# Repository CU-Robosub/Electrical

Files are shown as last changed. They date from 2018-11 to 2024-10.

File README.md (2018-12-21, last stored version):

# Electrical
All PCBs for the CU Boulder RoboSub team along with datasheets and archives from previous years.
### Datasheets
Collection of datasheets for all major PCB components
### Electrical_Archive
PCB Schematics, Layouts, and Libraries from previous years
### Hydrophone_Board
Design documents for the Hydrophone Board
### Merge_ESC_Board
Design documents for the Merge/ESC Board
### Power_Embedded_Board
Design documents for the Power/Embedded System Board
### Pneumatics_Board
Design documents for the Pneumatics Actuator Board
### Libraries
All Schematic, Footprint, and Integrated Libraries for the boards

## Merge/ESC Board Datasheet Links
Merge/ESC board will contain the Merge Circuit and header plugs for the Pololu along with outputs for the PWM and power outputs for the Electronic Speed Controllers.
### Merge Circuit
1. [LTC4357 Datasheet](http://cds.linear.com/docs/en/datasheet/4357fd.pdf)
2. [IPT004 Datasheet](https://www.infineon.com/dgdl/Infineon-IPT004N03L-DS-v02_00-EN.pdf?fileId=db3a30433e9d5d11013e9e0f382600c2)
### Current Monitor
1. [AD8217 Datasheet](http://www.analog.com/media/en/technical-documentation/data-sheets/AD8217.pdf)
### Kill Switch
1. [IRLR6225 Datasheet](https://www.infineon.com/dgdl/irlr6225pbf.pdf?fileId=5546d462533600a40153566d99bc26c1)

## Power/Embedded Board Datasheet Links
### 5V Converter
1. [R-78E5-0.5 Datasheet](https://www.recom-power.com/pdf/Innoline/R-78Exx-0.5.pdf) 
2. [AD8217 Datasheet](http://www.analog.com/media/en/technical-documentation/data-sheets/AD8217.pdf)
### 12V Converter
1. [Digikey](https://www.digikey.com/product-detail/en/tdk-lambda-americas-inc/I6A4W020A033V-003-R/285-2669-ND/6605122)
2. [Datasheet](https://www.us.tdk-lambda.com/ftp/specs/i6a4w_datasheet.pdf)
### 9V and 19V Converter
1. [LTC3780 Datasheet](http://cds.linear.com/docs/en/datasheet/3780ff.pdf)
2. [LTC3780 LTSpice](http://www.linear.com/product/LTC3780)
3. [BUK6212 Datasheet](https://assets.nexperia.com/documents/data-sheet/BUK6212-40C.pdf)
4. [MMSZ5230B Datasheet](https://www.diodes.com/assets/Datasheets/ds18010.pdf)
5. [MBRS340 Datasheet](https://www.mouser.com/ds/2/308/MBRS340-1120985.pdf)
6. [IN5819 Datasheet](http://www.kesenes.com/pdf/1n5817-1n5819.pdf)
7. [SRR1240 Datasheet](https://www.bourns.com/docs/Product-Datasheets/SRR1240.pdf)
8. [AD8217 Datasheet](http://www.analog.com/media/en/technical-documentation/data-sheets/AD8217.pdf)
### 48V Converter
1. [LTC3958 Datasheet](https://www.analog.com/media/en/technical-documentation/data-sheets/3958fa.pdf)
2. [LTC3958 LTSpice](http://www.linear.com/product/LT3958)
3. [IHLP-6767DZ-11 Datasheet](http://www.vishay.com/docs/34306/lp67dz11.pdf)
4. [AD8217 Datasheet](http://www.analog.com/media/en/technical-documentation/data-sheets/AD8217.pdf)
5. [MBRS360](https://www.onsemi.com/pub/Collateral/MBRS360T3-D.PDF)
### Embedded System
1. [MSP432P401R](http://www.ti.com/lit/ds/symlink/msp432p401r.pdf)
2. [DMN1019USN](https://www.diodes.com/assets/Datasheets/DMN1019USN.pdf)
3. [RGB LED Strip](https://www.sparkfun.com/products/12021)
4. [R-78E3.3-1.0](https://www.recom-power.com/pdf/Innoline/R-78Exx-1.0.pdf)
5. [JTAG Connector Digikey](https://www.digikey.com/product-detail/en/samtec-inc/FTSH-105-01-L-DV-K-TR/SAM13165CT-ND/8827920)
6. [JTAG Connector Datasheet](http://suddendocs.samtec.com/prints/ftsh-1xx-xx-xxx-dv-xxx-xxx-mkt.pdf)
7. [FTDI FT230X](https://www.ftdichip.com/Support/Documents/DataSheets/ICs/DS_FT230X.pdf)
8. [ABS25 Crystal Low Freq](https://abracon.com/Resonators/abs25.pdf)
9. [ABLS Crystal High Freq](https://abracon.com/Resonators/abls.pdf)
10. [Push Button Digikey](https://www.digikey.com/product-detail/en/te-connectivity-alcoswitch-switches/FSM101/450-1157-ND/701084)

## Pneumatics Board Datasheet Links
1. [MSP432P401R](http://www.ti.com/lit/ds/symlink/msp432p401r.pdf)
2. [JTAG Connector Digikey](https://www.digikey.com/product-detail/en/samtec-inc/FTSH-105-01-L-DV-K-TR/SAM13165CT-ND/8827920)
3. [JTAG Connector Datasheet](http://suddendocs.samtec.com/prints/ftsh-1xx-xx-xxx-dv-xxx-xxx-mkt.pdf)
4. [ABS25 Crystal Low Freq](https://abracon.com/Resonators/abs25.pdf)
5. [ABLS Crystal High Freq](https://abracon.com/Resonators/abls.pdf)
6. [FDY300NZ](https://www.fairchildsemi.com/datasheets/FD/FDY300NZ.pdf)
7. [R-78E3.3-1.0](https://www.recom-power.com/pdf/Innoline/R-78Exx-1.0.pdf)

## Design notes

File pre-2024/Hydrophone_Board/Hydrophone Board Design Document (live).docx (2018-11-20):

# CU RoboSub team

CU Robosub team

(date of release)

Hydrophone board

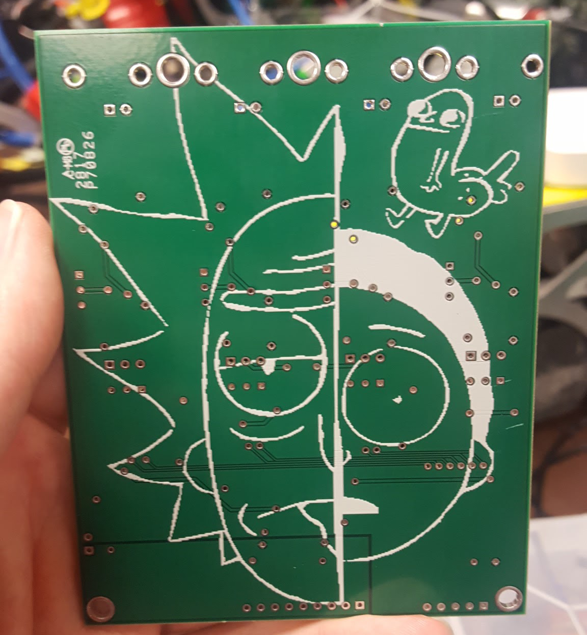
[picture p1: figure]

# Index

Abstract 3

Design Requirements 3

Design Overview 3

Previous designs 3

System Implementations 4

Power System 4

Active Filter 4

Amplification stage 4

ADC Sampling 4

System status 4

Known Issues 4

Appendix 4

# Abstract

This document will describe the standard documentation elements for the electrical design team. It is broken up into multiple sections that can be used or not used as is need. There will be release versions of this document as well as a “live” version. Release versions will be prefixed with the date of release (ie 2018-3-6-design-document-Format.pdf) and will be exported as PDF files. By keeping a live and release versions available members will continually be able to change, append, and add sections as is needed. Release versions will be tied to a particular version of the board that is manufactured.

# Design Requirements

In this section the requirements for each board will be described. This can be done with:

- Bullet points
- That describe each requirements

Description | Specifications
Or with a table | That can go into much greater detail about individual needs for each requirement

# Design Overview

This section will give the overall description of how all the different systems on the board work together. Not going into great detail on each individual section but any seasoned electrical engineer should be able to understand the entire system from this section alone.

## Previous designs

This section will give a high level description of previous designs and what was changed with this version. For new boards this is not necessary but for any revisions it will be required to look at previously released documentation and provide a description of which (if any) systems have been changed. If no systems have been changed describe why the board is being re-made.

# System Implementations

These sections will be made up of the technical information about each sub system. They should be sufficiently descriptive for a novice electrical engineering to be able to reference the information provided to learn how the systems work. This is the Section where you find the most errors in your work because as you try to justify your design decisions you may realise that you have made some incorrect assumptions. It will also give the team lead who will review this the opportunity to check on your thought process and make sure you are making the right design choices

## Power System

Basic LDO stage for getting needed power rails for adc, and filter stage

## Active Filter

Since the

## Amplification stage

Information about that

## ADC Sampling

Information about the Maxim board

# System status

This section is dedicated to describing the status of the system. What version is it on where is it in the production schedule.

# Known Issues

The board did not sample properly due to an issue with grounding of the negative line of the

# Appendix

This is where you will store all of your information on which parts were used and links to their data sheets. Also links to where the Altium files can be found (they should be within the folder this document is stored in) and any citations to resources you found useful in the design process for this part.

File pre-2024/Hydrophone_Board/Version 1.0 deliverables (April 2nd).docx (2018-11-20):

- Board schematics: complete
- Design document: incomplete
  - Abstract incomplete
  - Design requirements incomplete
  - Design Overview incomplete
  - Previous design incomplete
    - Hydrodynamix
  - Implementations incomplete
    - Power System incomplete
      - Schematic
      - Part descriptions
    - Active Filter incomplete
      - Filter response diagrams
      - Part selection
    - Amplification stage incomplete
      - Part selection
      - Gain choice
      - Gain switching chip
    - ADC sampling incomplete
      - MAXIM 11043
      - Reference the design choices
  - Known issues incomplete
    - Many lol
  - Appendix incomplete
    - Reference parts
    - Reference Python package
    - Reference fpga project

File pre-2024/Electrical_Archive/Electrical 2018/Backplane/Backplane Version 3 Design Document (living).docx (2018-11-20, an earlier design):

CU RoboSub Team

8/15/2018

Backplane V3

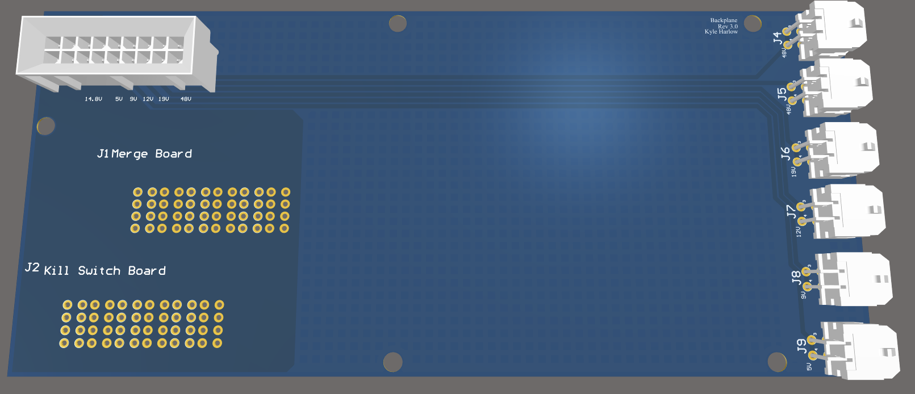
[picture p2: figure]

Abstract 3

Design Requirements 3

Design Overview 3

Previous designs 3

System descriptions 4

System status 4

Known Issues 4

Appendix 5

# Abstract

The backplane supports all of the other PCBs attached to it and properly routes power to those boards. The backplane also routes power to all other systems on the sub through a variety of headers and passive components.

# Design Requirements

Using a variety of molex connectors, passive traces, and polygon planes, the backplane must:

- Receive input power and ground connections from the merge board.
- Route proper connections for power and ground to every other board without thermal issues.
- Export the power board’s voltage lines to an accessible place in the sub, so wires can be routed to proper locations.

# Design Overview

This entirely passive board will use molex connectors and heavier copper pours to achieve all design requirements listed above. The Merge Board and ESC Board will connect using Molex’s EXTreme EnergetiC Modular Right-Angle and Vertical Plug Assemblies since they only need to pass a lot of power between each other. The Power Board will connect to the backplane through Molex’s Micro-Fit BMI Dual Row Receptacle Header with 18 pins because it has to pass several voltage lines as well as receive enough power and ground connections for proper power delivery. For the conversion from PCB traces to wires, we used the 4 pin Molex MiniFit Juniors at the end of the power board. Despite their size, these can handle the current requirements our systems need, and with their locking clips, they provide safe connections to the rest of the system.

## Previous designs

Previous designs of the backplane had no major issues, but the change to better connectors required a redesign. This redesign also allowed us to switch to higher oz copper which was a long term plan to allow for better thermals.

# System descriptions

Shown below is the completed backplane in Altium. Red represents top layer traces while blue represents bottom level traces. To properly route power without overheating, this board was manufactured with 6oz copper, which physically compresses more copper onto the pcb traces and planes so it takes longer to heat up. This increase of copper allows for smaller trace widths from the power board connector, at the top of the picture, to the molex connectors, at the far right of the picture.

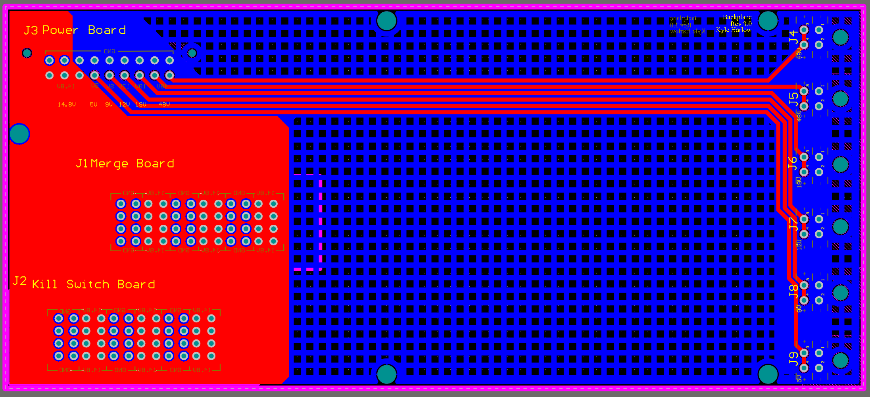
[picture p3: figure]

Due to this board being entirely passive and still quite large, the ground plane, on the bottom layer, was latticed in unused areas. This reduces the amount of wasted copper while still providing proper connections, resistance from warping, and some noise shielding. Besides the molex vias, full standoff screw holes were created for proper usage in the sub on the electrical rack. This was mainly for support and rigidity since none of the electrical rack was conductive.

# System status

This system was completed and ran successfully on the 2018 sub Leviathan. No major issues were experienced after soldering.

# Known Issues

- Board potentially not needed. If kill switch/esc board is removed, the molex connectors can be moved to the power and merge boards to save cost and space. The power and merge boards can then be directly connected to transfer power properly.
- Incorrect via sizes for molex headers
- Wrong initial orientation of power board’s header
- Molex connectors do not provide enough support to boards without electrical rack

# Appendix

Backplane MiniFit Juniors - https://www.molex.com/molex/products/datasheet.jsp?part=active/0039300040_PCB_HEADERS.xml

Power Board Micro-Fit - https://www.molex.com/molex/products/datasheet.jsp?part=active/0447640801_PCB_RECEPTACLES.xml

Merge and ESC - https://www.molex.com/molex/products/datasheet.jsp?part=active/1721860010_PCB_RECEPTACLES.xml

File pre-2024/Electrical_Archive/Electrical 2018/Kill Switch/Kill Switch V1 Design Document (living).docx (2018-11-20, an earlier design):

# CU Robosub team

# 8/29/2018

# Kill Switch/ESC Board

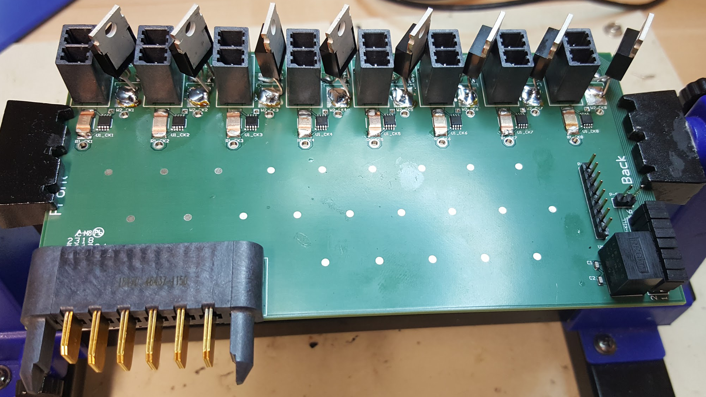
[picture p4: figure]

Abstract 3

Design Requirements 3

Design Overview 3

Previous designs 3

System descriptions 3

Recom and Kill Switch 4

System status 4

Known Issues 5

Appendix 5

# Abstract

The kill switch board controls all power to the ESC modules and therefore the motors. This board can cut the power to the motors based off the kill switch’s state, allowing voltage to pass through the onboard mosfets to ground or holding the voltage high so the motors have nothing to work off of.

# Design Requirements

The kill switch board must:

- Receive input power and ground connections from the backplane.
- Route proper connections for power and ground to every ESC module.
- Use the kill switch’s state to properly turn off the motors.
- Not overheat from the amount of current passing through it.

# Design Overview

All of the ESC modules are controlled by N-channel mosfets that had their gate connected to a 5V line which could be broken by the kill switch. The mosfet’s controlled the motor’s connection to ground, so if the kill switch was active, then the motors would float at 14.8V with no way to draw current and turn. When the kill switch was disabled, the 5V line would activate the mosfets which allowed the motors to create a complete circuit and rotate as desired by the Pololu controller.

## Previous designs

Previously, this board was combined with the merge board due to the power requirements of the motors and the sub. The previous design was functional, but there was too much power on that pcb, without proper thermal considerations, so it started melting off soldered components. The mosfets also were not reliable and several broke from various incidents of polarity and misuse.

# System descriptions

Shown below is the completed kill switch board design. Red represents top layer traces while blue represents bottom level traces. This board ended up being a four layer PCB in order to route power and ground planes more efficiently and to potentially improve thermals with extra copper pours.

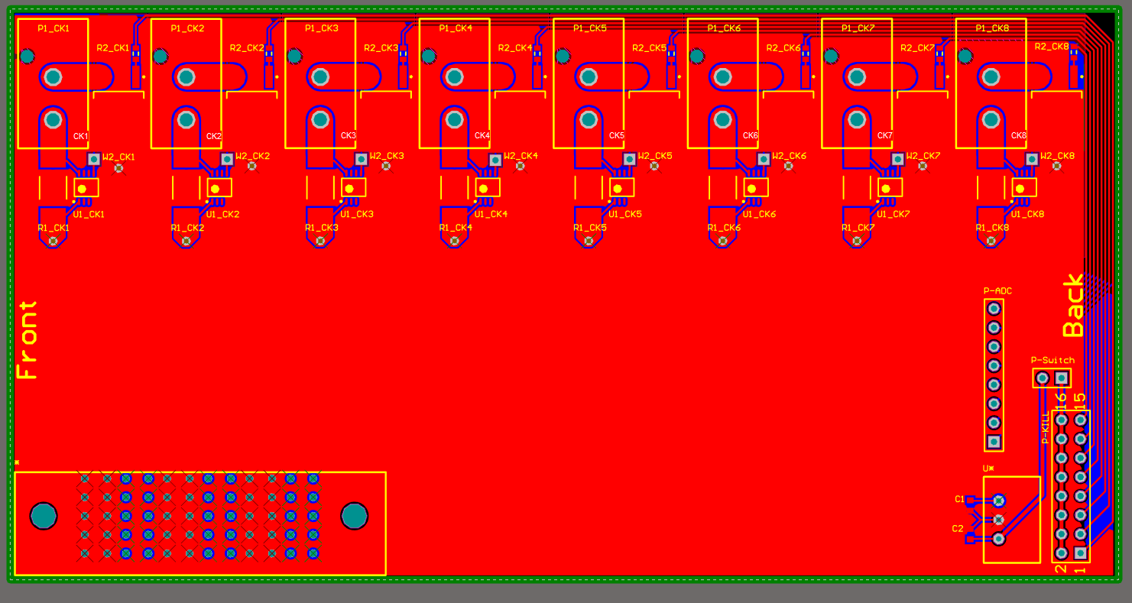
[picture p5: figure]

The top two layers of this board were reserved for the ground plane so that the mosfets could easily connect to the plane and pass as much current to it as needed. These planes were connected through a lattice of vias, not shown in the picture, to assure proper connections and thermal availability. The bottom two layers were set as the power plane that connected to the through-hole molex connectors. These connectors were for the ESC’s to connect to in a polarized way that couldn’t reverse polarity on accident like the previous bullet connectors. These bottom two planes were connected by more latticed vias to assure proper power distribution throughout the board. AD8217s were used as current monitors for the ESC inputs.

## Recom and Kill Switch

In the bottom right corner of this board a recom 5V converter was provided to create a gate signal for all of the mosfets. This voltage line immediately connected to the kill switch so that we could control the gate signals. The kill switch was soldered between the two horizontal vias labeled as p-switch. From the other end of the killswitch we created a row of jumper headers to connect all of the gates to the signal in an easy way. Due to the Recom’s max current specs and good electrical practices, we also implemented 1KOhm resistors in series in front of the gates to not kill the mosfets if any power spikes did occur for any reason.

# System status

This system was completed and ran successfully on the 2018 sub Leviathan. No major issues were experienced after soldering.

# Known Issues

- This board is potentially not needed. Due to the Pololu Motor Controller’s reset pin, we can cut all motors without this board. Resetting the Pololu will remove all data inputs for the ESC’s and they will stop providing power to the motors.
- Wrong mosfet connections. Flip source and drain routing for proper function
- Schematics only show boxes for the mosfets instead of their internal design. (This created the wrong mosfet orientation problem)
- Forgotten pulldown resistor from mosfet gates to GND
- Kill Switch soldering vias were easily stripped/deplated. Switch to Molex connectors

# Appendix

N-Channel Mosfets: https://www.digikey.com/product-detail/en/infineon-technologies/IRLR6225TRPBF/IRLR6225TRPBFCT-ND/2538170

5V converter: https://www.digikey.com/product-detail/en/recom-power/R-78E5.0-0.5/945-1648-5-ND/2834904

ESC Connectors:

https://www.molex.com/molex/products/datasheet.jsp?part=active/0768290102_PCB_HEADERS.xml

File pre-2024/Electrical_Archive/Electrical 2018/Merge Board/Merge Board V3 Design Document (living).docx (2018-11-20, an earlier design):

# CU Robosub team

# 9/1/2018

# Merge Board

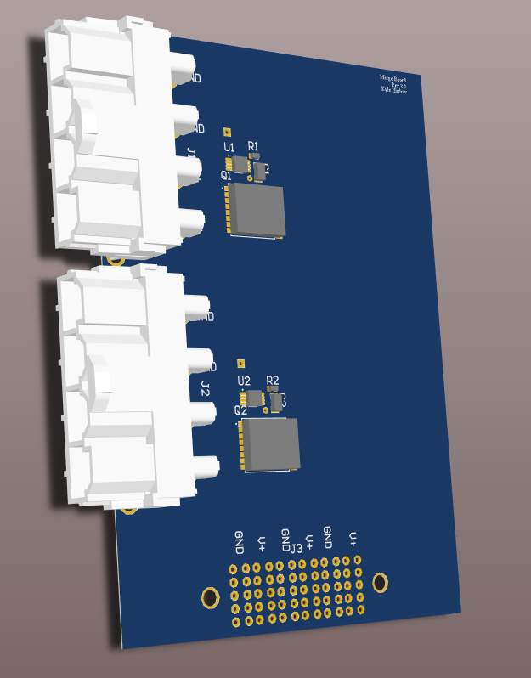
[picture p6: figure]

Abstract 3

Design Requirements 3

Design Overview 3

Previous designs 3

System descriptions 4

System status 5

Known Issues 5

Appendix 5

# Abstract

The merge board controls all input power to the sub from the two batteries. This board also balances the battery draw so that they drain equally and don’t start charging each other or dropping too quickly into dangerous low voltage states.

# Design Requirements

The merge board must:

- Receive input power and ground connections from the battery pods.
- Route proper connections for power and ground to the backplane.
- Not overheat from the amount of current passing through it.

# Design Overview

The batteries connect to the merge board through Molex CONNECTORS that can handle the large amount of current flowing through them. From there, the batteries are funnelled through high power mosfets from Infineon Technologies that can be turned off by commands from LTC4357s. The two LTC4357s perform OR operations to use the battery with the highest voltage, so that the sub will drain the fullest battery first. From there, the two battery inputs are merged into a 3oz copper plane and connected to the backplane for the other systems to use.

## Previous designs

Old merge boards used to combine both the kill switch/esc board and the merge board. This was to save space and cost, but due to oversights in copper thickness and design, these boards did not work as intended. Old desings had too small of copper necks from the battery connectors to the high power mosfets, so they would significantly heat up and potentially melt components off of the board. The old designs also used unreliable connectors to attach the battery leads which created worries for shorting and current throughput.

# System descriptions

Shown below is the completed kill switch board design. Red represents top layer traces while blue represents bottom level traces. This board ended up being a two layer PCB with 3oz copper pours in order to route power and ground planes more efficiently and to significantly improve thermals. While it would have been better, 6oz copper was not used due to the clearances the LTC4357 and mosfet’s pads need to work properly. To compensate for this, large power and ground planes were used to dissipate the extra heat.

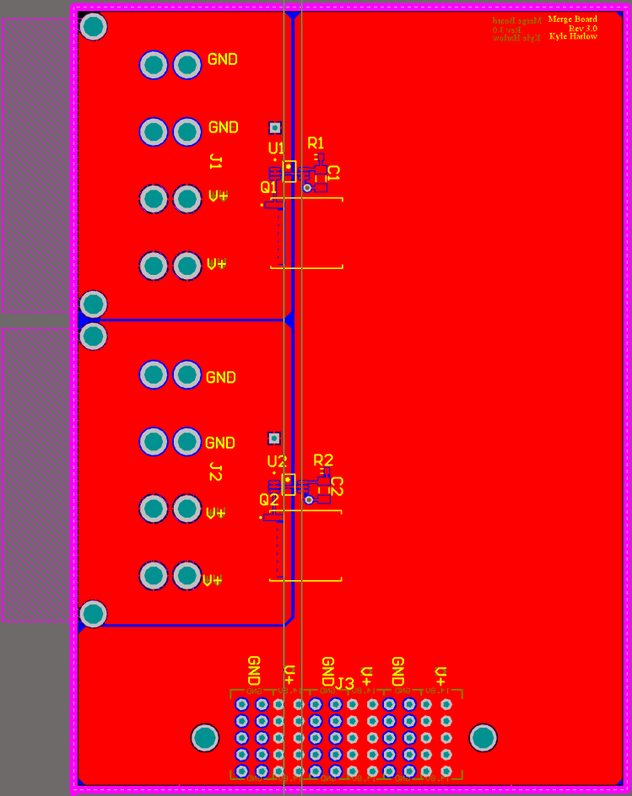
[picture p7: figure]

# System status

This system was completed and ran successfully on the 2018 sub Leviathan. No major issues were experienced after soldering.

# Known Issues

- This board is too tall. With the electrical rack, the clearance from this board to the acrylic tube is small enough to cause issues when taking the sub apart.
- The connector to the backplane cannot support the board completely and will get looser overtime.

# Appendix

Input Mosfets: https://www.digikey.com/products/en?keywords=IPT004N03LATMA1CT-ND

LTC4357: https://www.digikey.com/products/en?keywords=LTC4357CMS8%23PBF-ND

MiniFit Sr. Headers: https://www.molex.com/molex/products/datasheet.jsp?part=active/0428204214_PCB_HEADERS.xml

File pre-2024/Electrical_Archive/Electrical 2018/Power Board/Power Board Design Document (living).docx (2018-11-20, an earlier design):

Cover Page

CU Robosub team

(date of release)

Name of the Board

Add a nice picture here

Abstract 3

Design Requirements 3

Design Overview 3

Previous designs 3

System descriptions 4

5V line 5

12V line 6

19V line 7

48V line 7

System status 8

Known Issues 8

Appendix 8

# Abstract

The Power conversion board takes in 14.8V from the merge circuit board through the backplane and converts it into various voltage levels to power each of the other electrical systems on the UAV. The power conversion board will also contain a microcontroller for current sensing.

# Design Requirements

Description | Specifications
5V line | 1A buck - No Peripherals Internal to Sub
12V line | 3A buck - Hydrophones, Pneumatic Systems, and Pressure Sensor
19v line | 4A boost - Computer
48V line | .5A boost - Down Cam
48V line | .5A boost - DVL Power

# Design Overview

#TODO give information about the parts used and the design process

## Previous designs

Design V1.0 was not of sufficient quality. It had no reverse bias protection which caused it to fail when brought to competition. (#TODO add details about parts used and what was done right I believe it was the LTC3958?)

# System descriptions

Shown below is the completed power design board. Red represents top layer traces while blue represents bottom level traces. Each subsystem will be described in full within their subsequent system descriptions

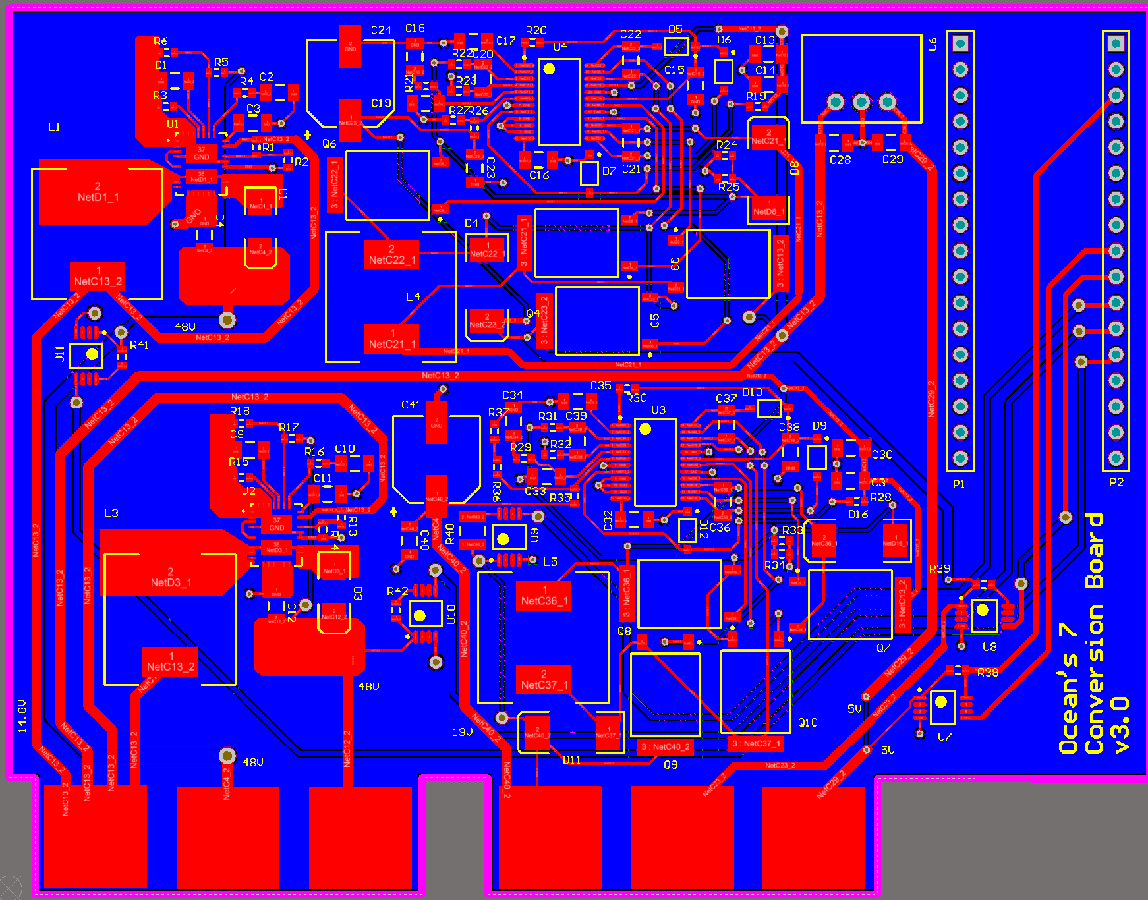
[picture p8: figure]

Figure 1: completed circuit board design

## 5V line

This systems consists of taking a R-78E-0.5 low cost switching regulator and adding a few decoupling capacitors to the input and output lines. Followed by a current sensing resistor with a AD8217 Analog Devices high resolution, zero drift current shunt monitor chip. This device utilizes a 5 mF sense resistor to measure current draw as linear voltage based on the current drop across the sense resistor.

Data sheets can be found in Electrical Research > Power Conversion Chips

AD8217.pdf

R -78Exx-0.5.pdf

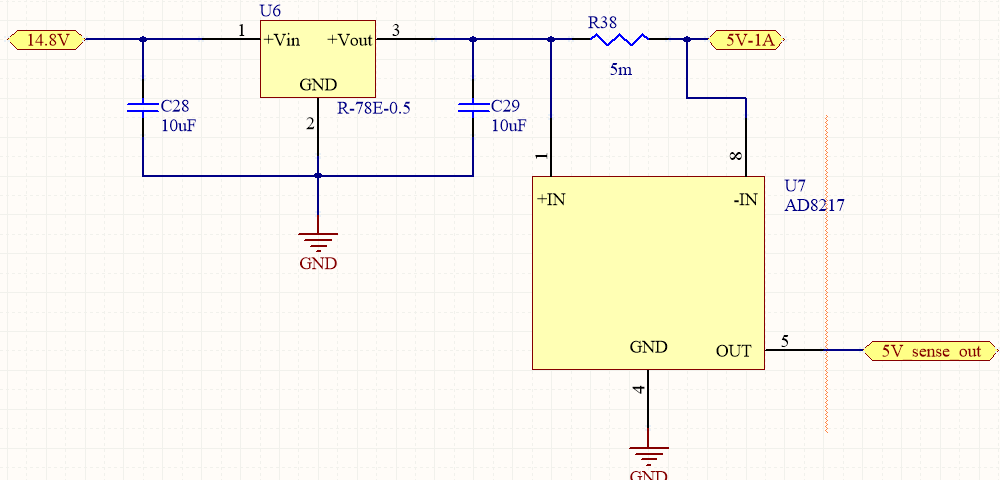
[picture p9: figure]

## 12V line

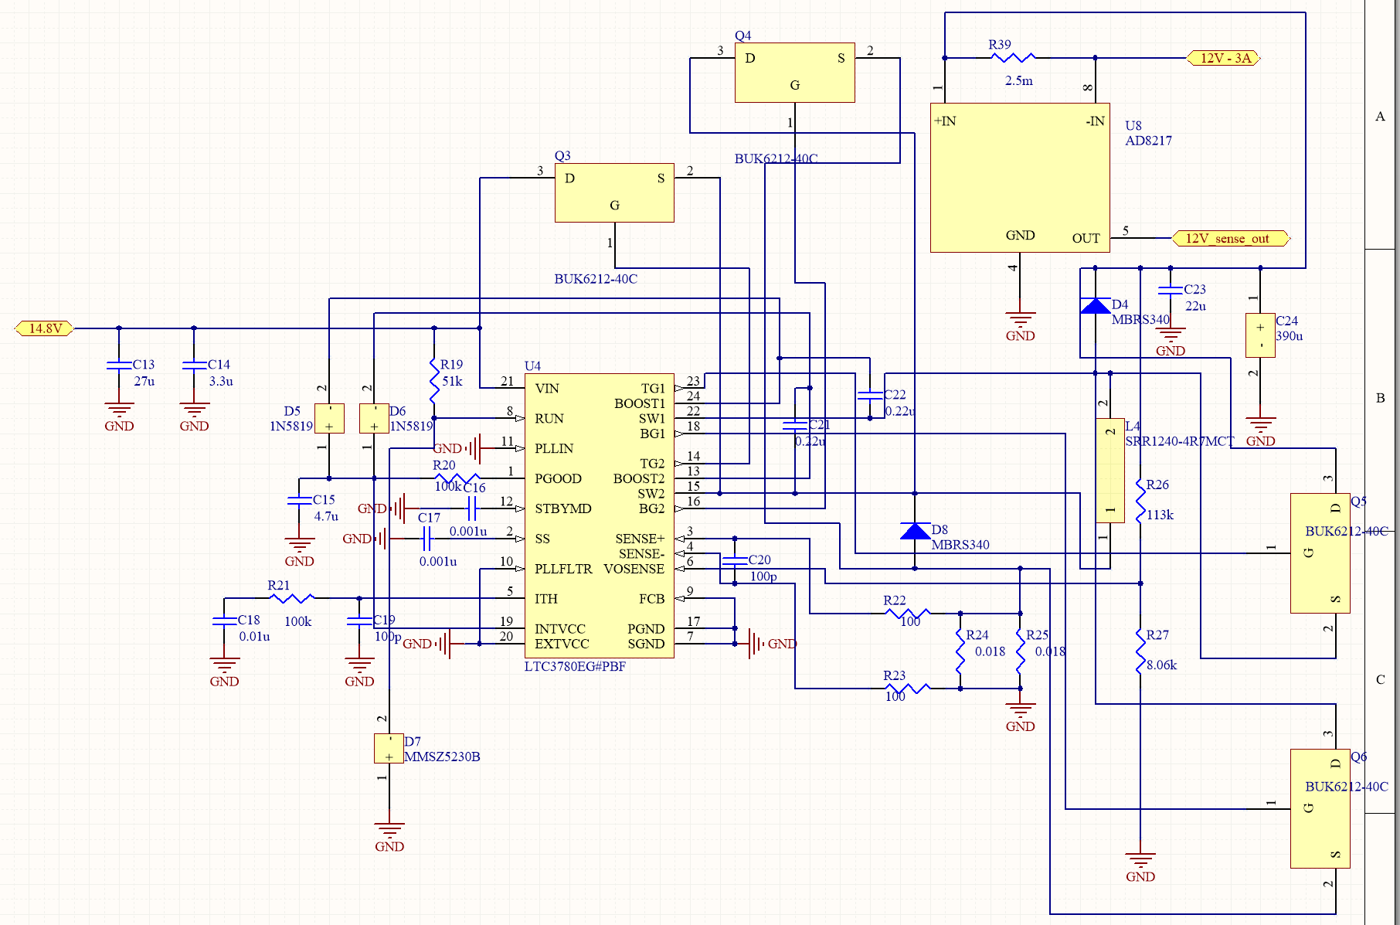
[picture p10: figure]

## 19V line

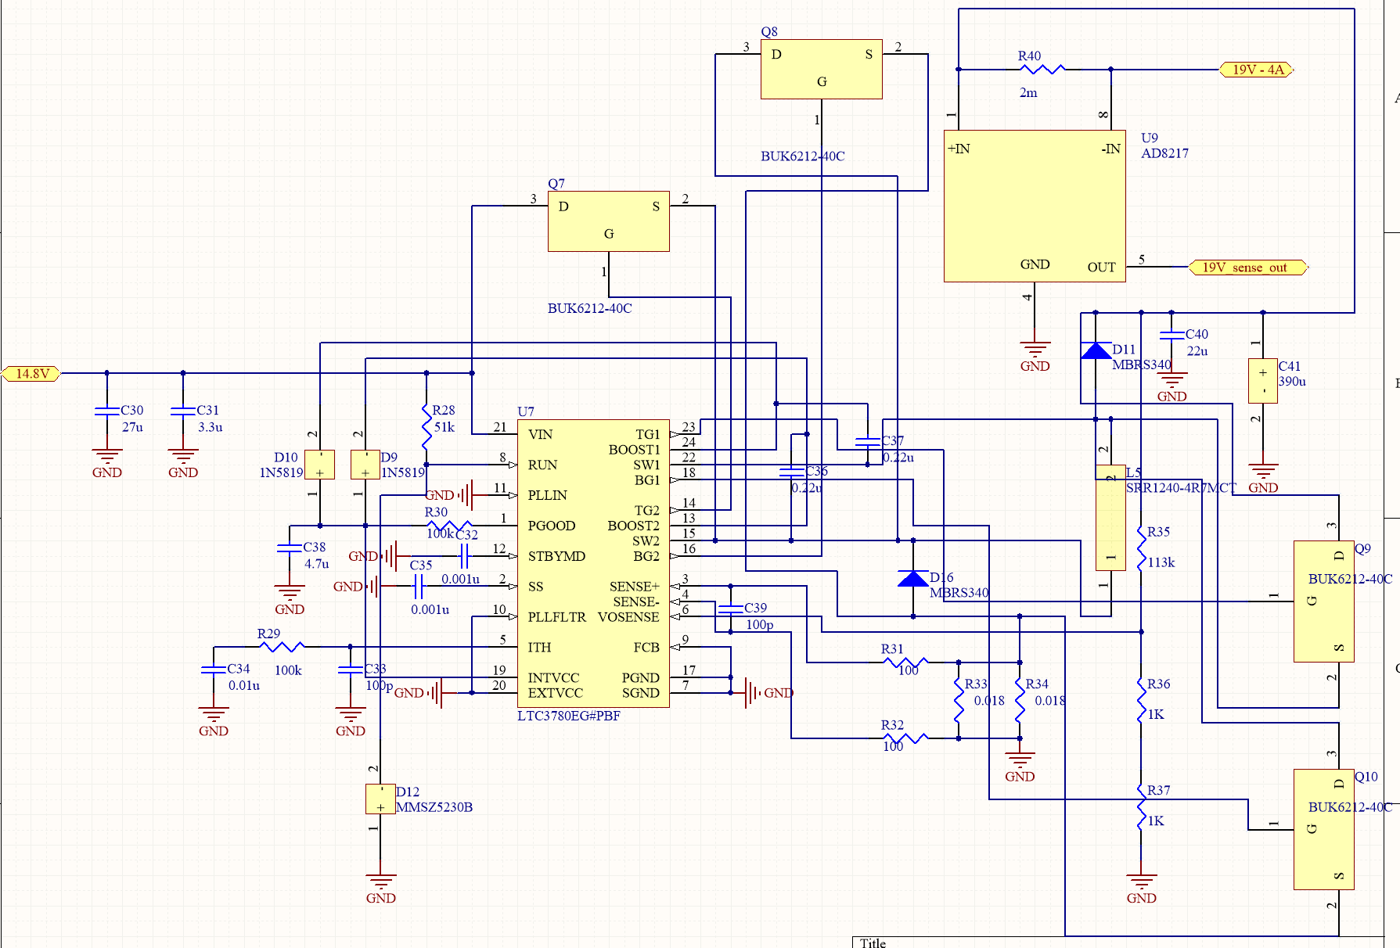
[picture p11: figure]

## 48V line

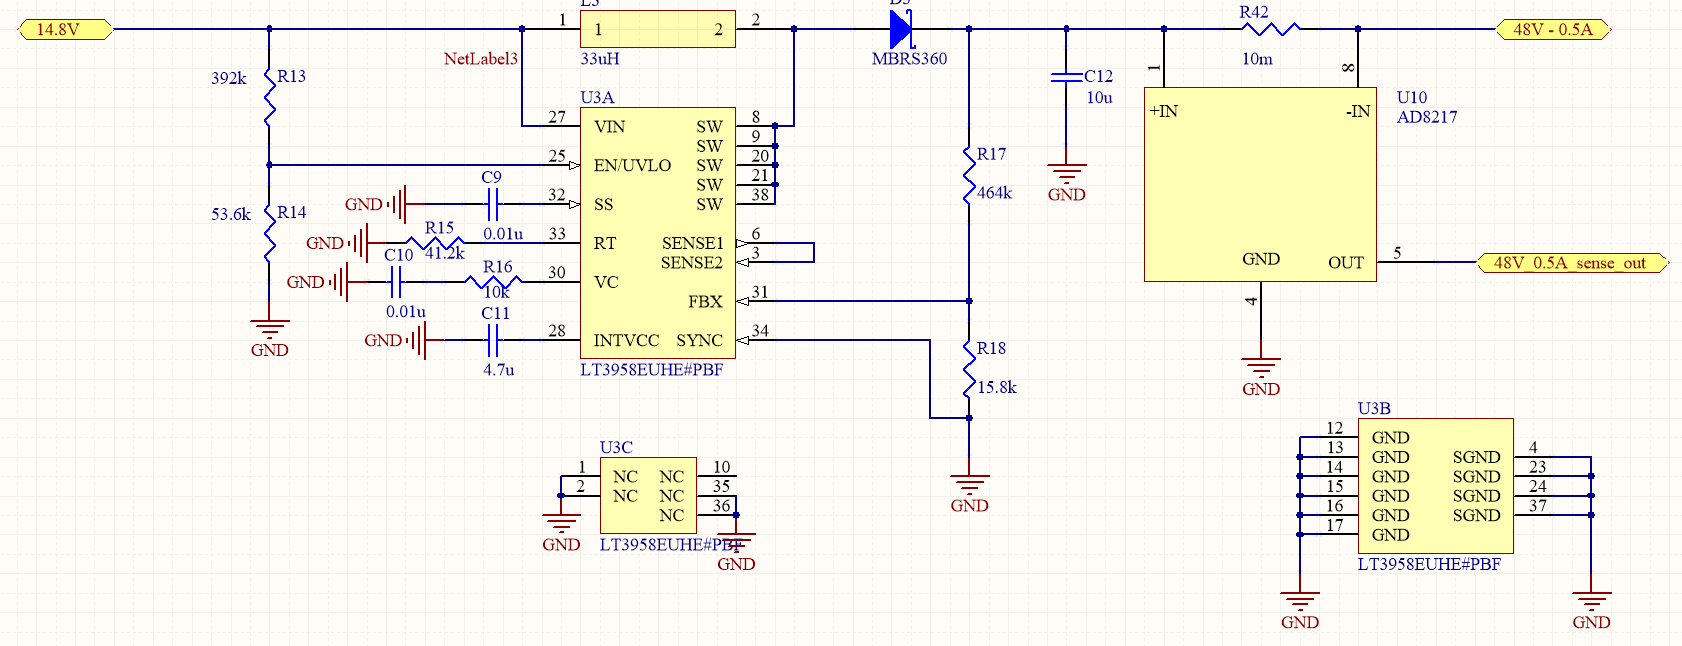
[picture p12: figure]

## Microcontroller Monitoring

# System status

This system was completed and ran successfully on the 2017 sub Leviathan.

# Known Issues

- Not able to properly monitor circuit health with arduino micro.
- No power management for proper startup and shutdown of power boards

# Appendix

This is where you will store all of your information on which parts were used and links to their data sheets. Also links to where the Altium files can be found (they should be within the folder this document is stored in) and any citations to resources you found useful in the design process for this part.

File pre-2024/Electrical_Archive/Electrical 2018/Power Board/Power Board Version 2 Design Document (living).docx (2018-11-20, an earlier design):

CU RoboSub Team

8/8/2018

Power Board V2

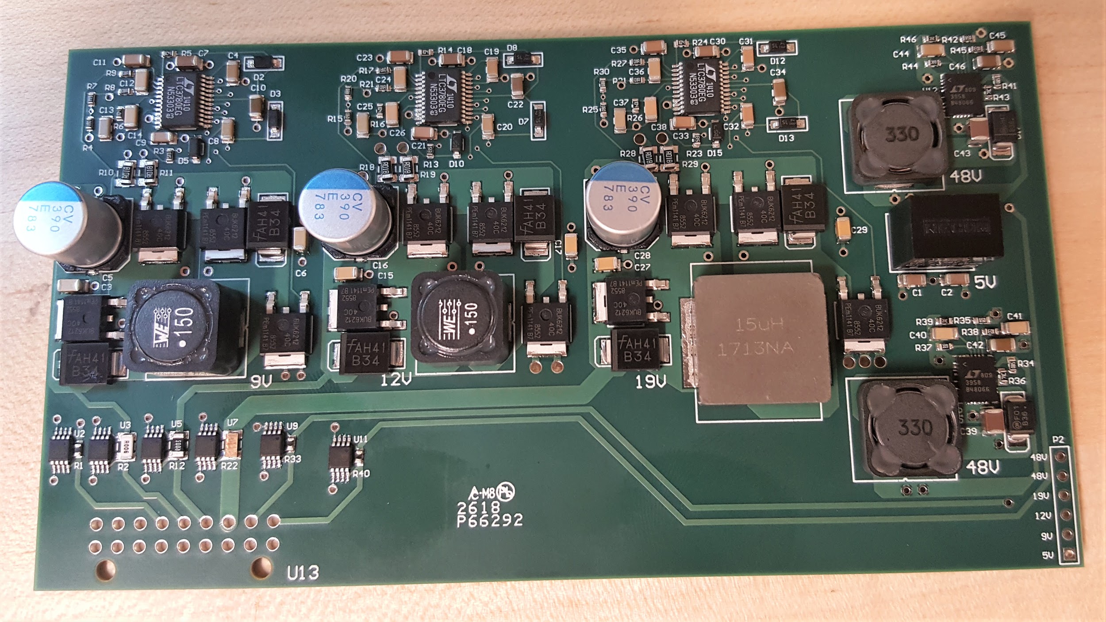
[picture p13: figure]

Abstract 3

Design Requirements 3

Design Overview 3

Previous designs 3

System descriptions 4

5V line 5

9V line 6

12V line 7

19V line 8

48V line 9

System status 9

Known Issues 9

Appendix 10

# Abstract

The power conversion board takes in approximately 14.8V from the merge circuit board through the backplane and converts it into various voltage levels to power each of the other electrical systems on the UAV.

# Design Requirements

Description | Specifications
5V line | 1A buck - Backup Line for Various Systems
9V line | 1A buck - Network Switch
12V line | 3A buck - Hydrophones, Pneumatic Systems, and Pressure Sensor
19V line | 4A boost - Computer
48V line | .5A boost - Down Camera with POE Injector
48V line 2 | .5A boost - DVL Power with ethernet splitting

# Design Overview

This board went through several revisions before this version was published. The revisions mostly involved reconfiguring layouts of the 9,12, and 19V lines along with redesigns to follow good PCB routing practices. These voltage lines used the LTC3780 controller with the recommended array of passive and active components. The two 48V lines used the recommended configurations for the LTC3958. These recommended designs can be found in the respective data sheets on Linear Technology’s website linked in the appendix.

## Previous designs

Design V1.0 was not of sufficient quality. It had no reverse bias protection which caused it to fail when brought to competition, along with several thermal, efficiency, and consistency issues. However, the buck and boost converters had quality designs and were continued into the second revision. Despite the good designs, the 19V line could not power a new computer, primarily due to components that could not handle the full 4A and incorrect current limiting resistors. The sub’s computer is a major component of the system so this board had to be redesigned for proper operation of the AUV.

# System descriptions

Shown below is the completed power board design. Red represents top layer traces while blue represents bottom level traces. This board ended up being a four layer PCB in order to route power and ground planes more efficiently and to potentially improve thermals with extra copper pours. The power plane is represented by the yellow plane and the ground is the cyan plane that covers the entire board. Each subsystem will be described in full within the subsequent sections.

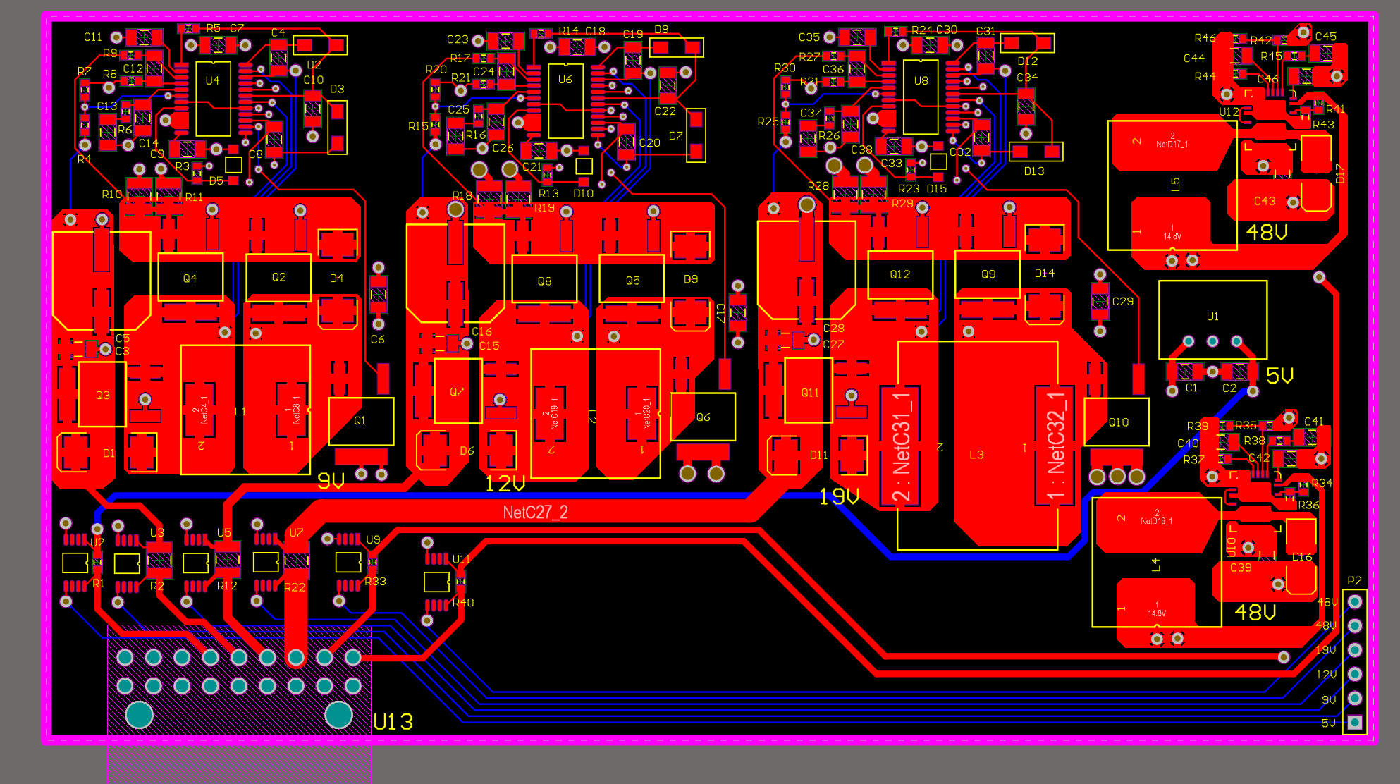
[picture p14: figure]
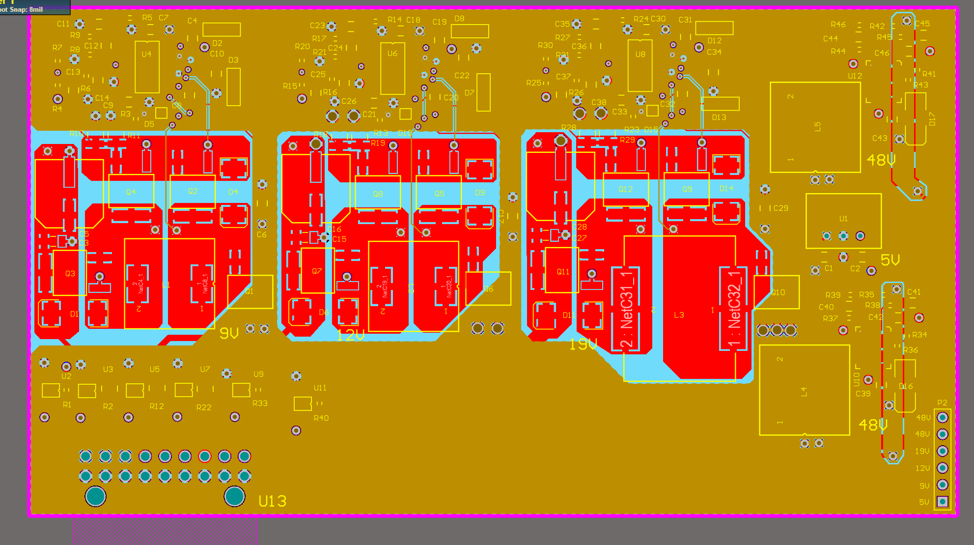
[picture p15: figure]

## 5V line

This systems consists of taking a R-78E-0.5 low cost switching regulator and adding a few decoupling capacitors to the input and output lines. Followed by a current sensing resistor with a AD8217 Analog Devices high resolution, zero drift current shunt monitor chip. This device utilizes a 10 mOhm sense resistor to measure current draw as linear voltage based on the current drop across the sense resistor.

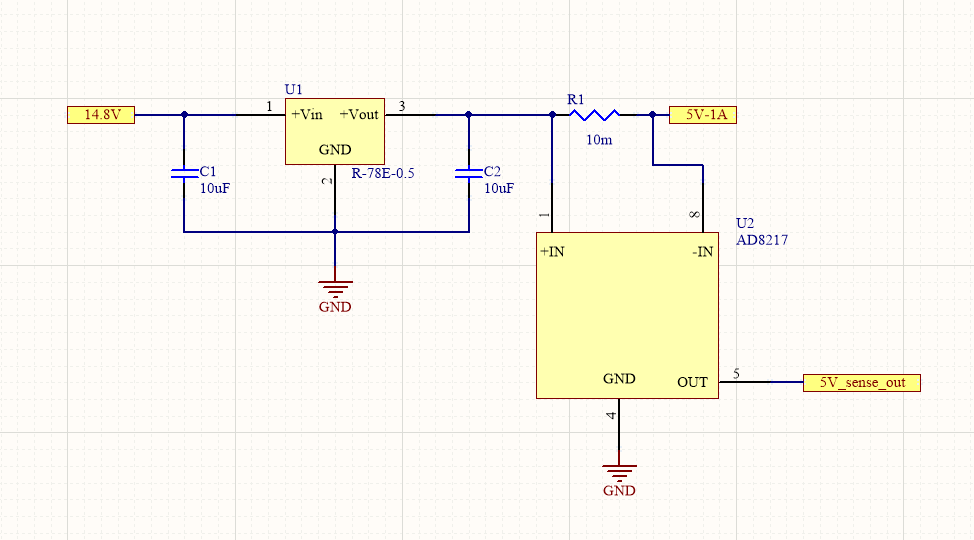
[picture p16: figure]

## 9V line

This systems consists of taking the LT3780’s recommended schematic, adding a few decoupling capacitors, and changing the Vosense resistors. The implemented Vosense resistors of 113kOhm and 11kOhm provide an output voltage of 9.02V. Reading the datasheet will be required for complete understanding of this IC. In brief, the voltage is modulated with an inductor and passed through external mosfets controlled by the IC’s oscillation cycles to allow for a variety of power requirements. This is all followed by a current sensing resistor with a AD8217. This device utilizes a 6mOhm sense resistor to measure current draw as linear voltage based on the current drop across the sense resistor.

The PCB layout of this circuit also follows the recommended design from the LT3780’s data sheet for optimal efficiency and ease of design. Due to the high current passing through some of the components, the component pad to polygon neck widths were increased from default, larger/duplicated vias were used to provide safe and sufficient power management, and output trace widths to the connector were increased based on online thermal and resistance calculators for PCB traces.

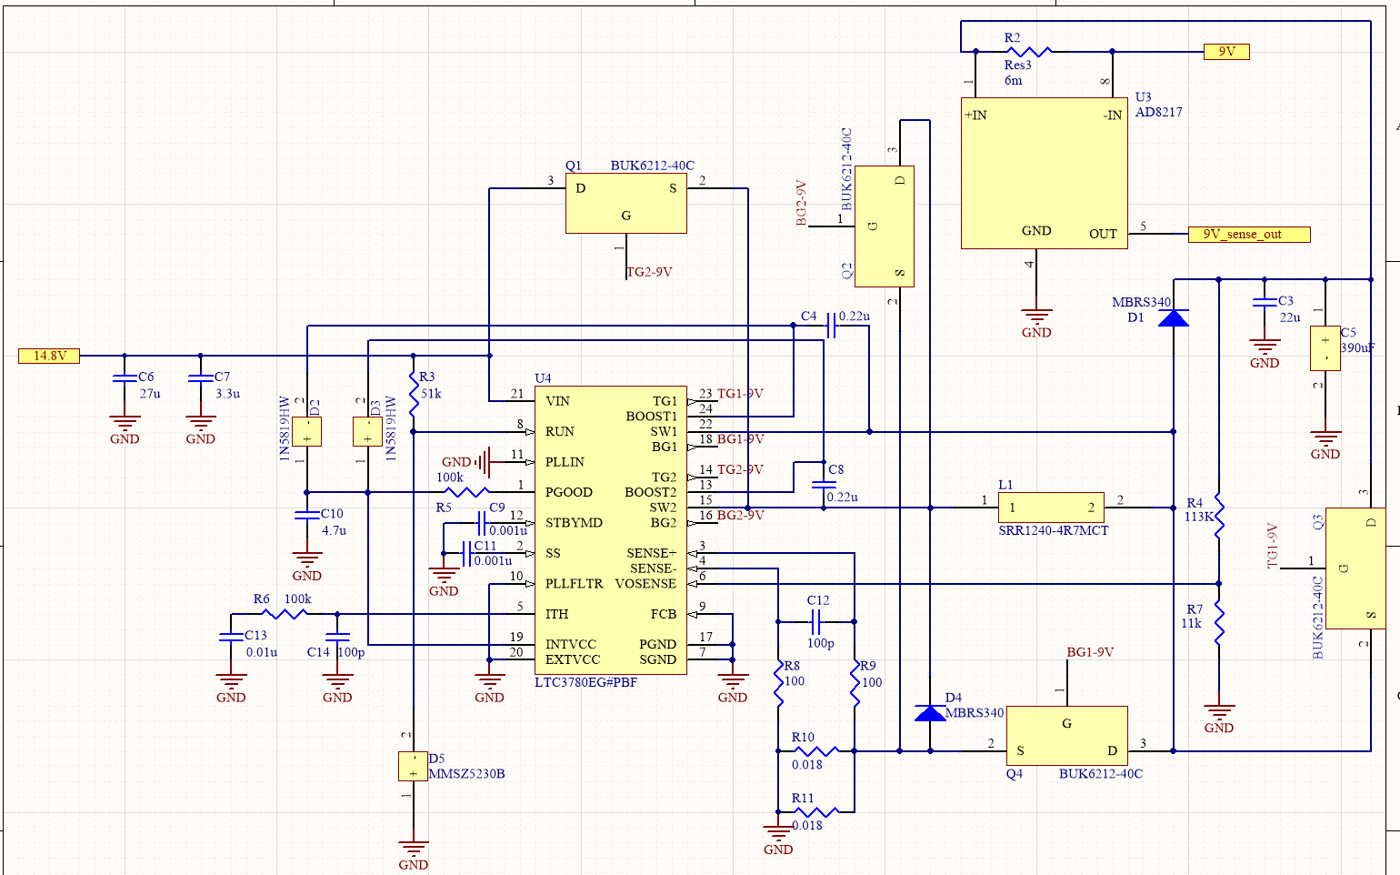
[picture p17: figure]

## 12V line

This systems consists of taking the LT3780’s recommended schematic, adding a few decoupling capacitors, and changing the Vosense resistors. The implemented Vosense resistors of 113kOhm and 8.06kOhm provide an output voltage of 12.02V. This line utilizes a 3mOhm sense resistor for its AD8217 to measure current draw as linear voltage based on the current drop across the sense resistor. The PCB layout of this circuit also follows the recommended design from the LT3780’s data sheet for optimal efficiency and ease of design. For further questions refer to the 9V line for a summary of this system since they are identical.

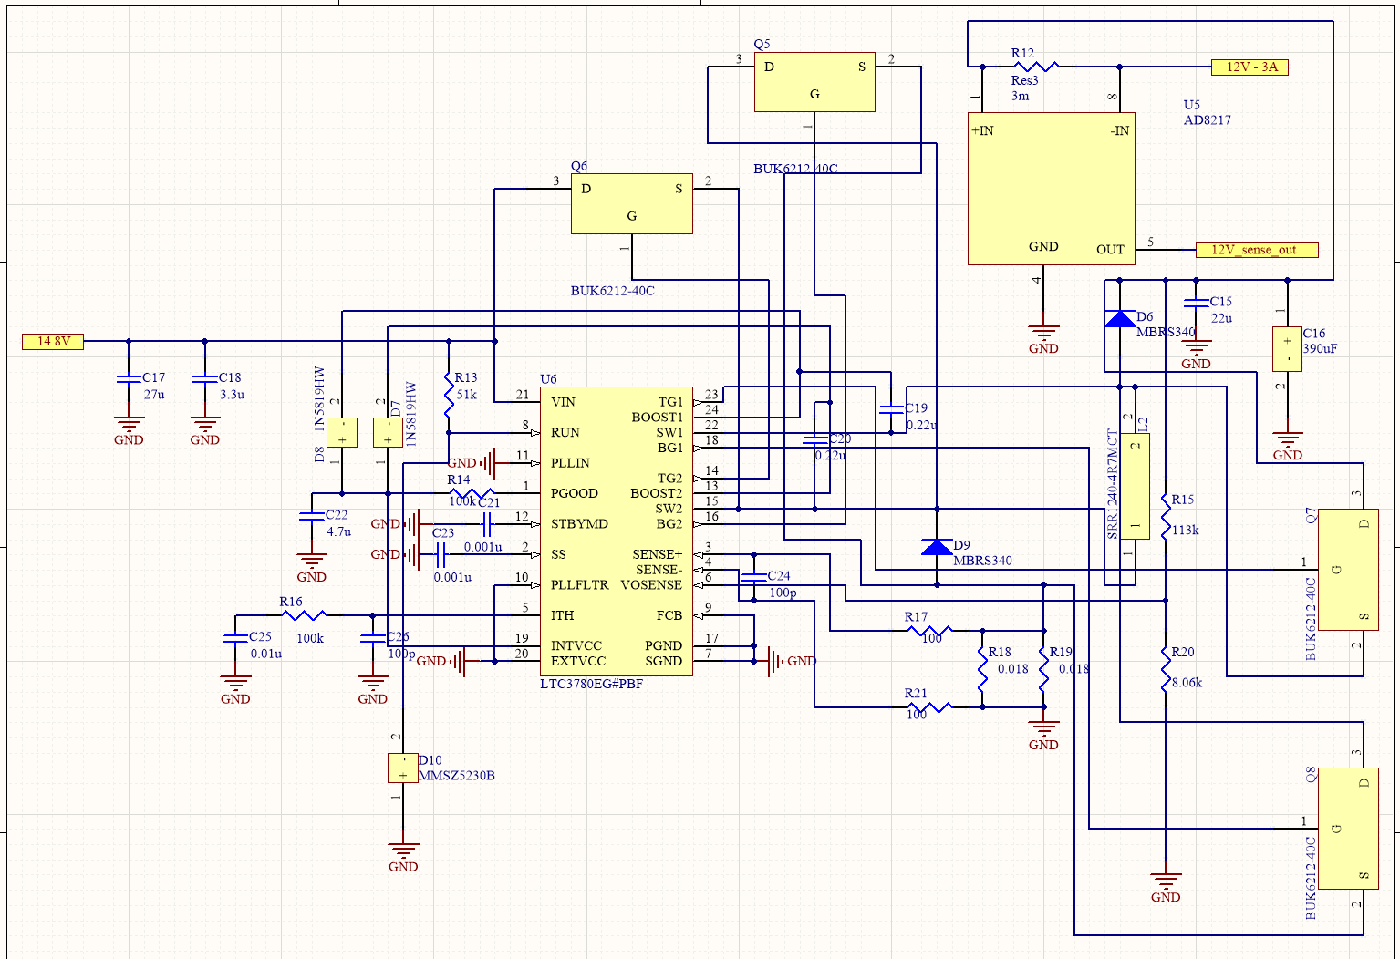
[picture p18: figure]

## 19V line

This systems consists of taking the LT3780’s recommended schematic, adding a few decoupling capacitors, and changing the Vosense resistors. The implemented Vosense resistors of 113kOhm and 4.99kOhm provide an output voltage of 18.92V. This device utilizes a 1mOhm sense resistor for its AD8217 to measure current draw as linear voltage based on the current drop across the sense resistor. The PCB layout of this circuit also follows the recommended design from the LT3780’s data sheet for optimal efficiency and ease of design. For further questions, refer to the 9V line for a summary of this system since they are identical besides the boost conversion.

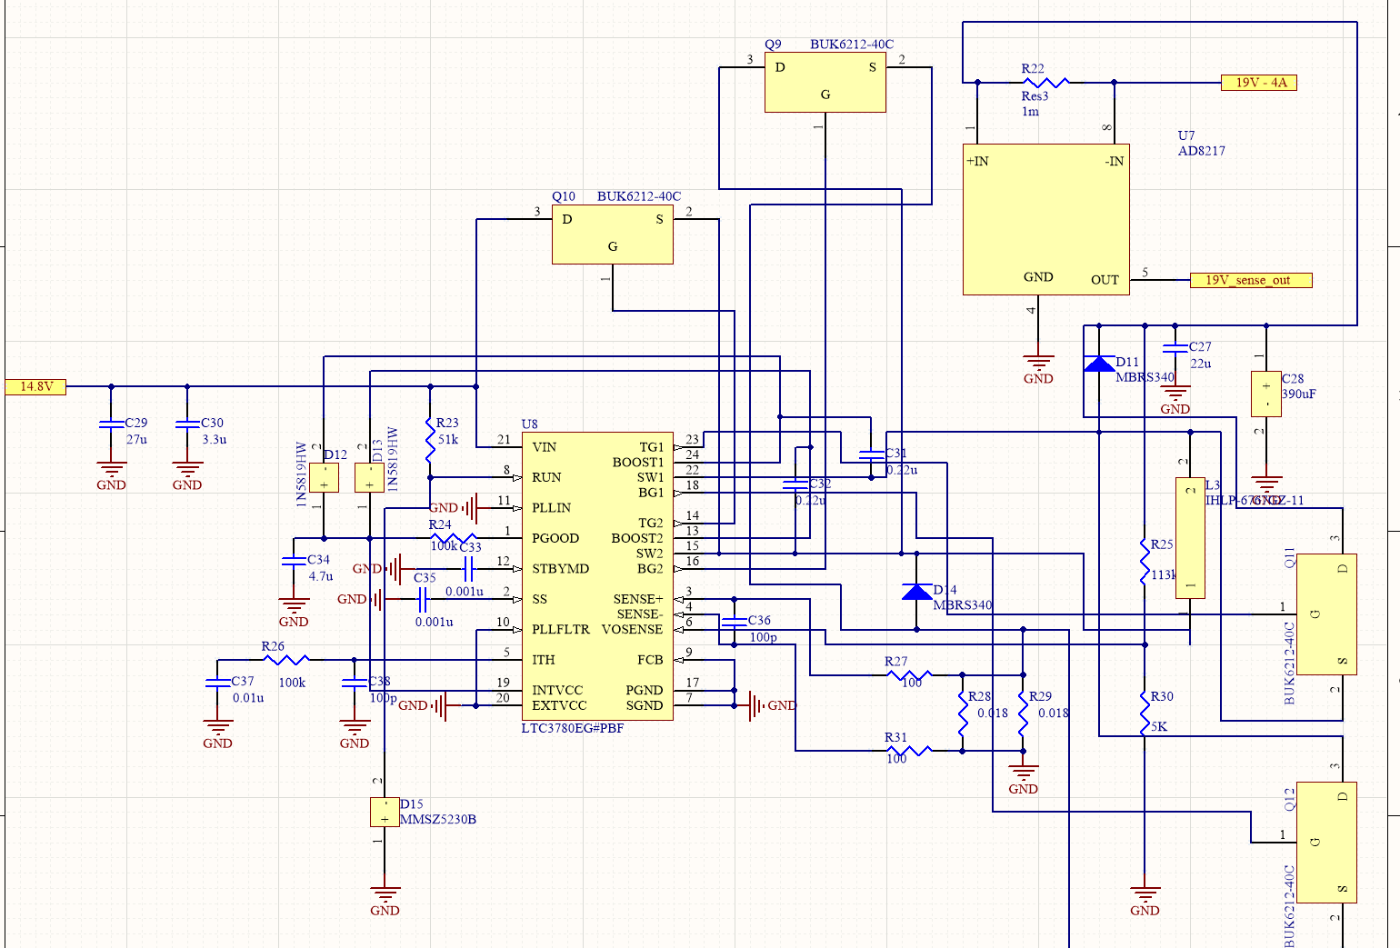
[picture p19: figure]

## 48V line

This systems consists of taking the LT3958’s recommended 48V schematic and adding a few decoupling capacitors. Reading the datasheet will be required for complete understanding of this IC. In brief, the voltage is modulated with an inductor and feedback loops through internal regulators, comparators, and a variety of oscillation cycles. This is all followed by a current sensing resistor with a AD8217. This device utilizes a 10 mOhm sense resistor to measure current draw as linear voltage based on the current drop across the sense resistor.

The PCB layout for this system is fully detailed with pictures in the LT3958’s data sheet, so implementation is fairly straightforward. We implemented multiple polygon pours that had no thermal relief/component pad to polygon necks due to the tight clearances of the LT3958 and the system being limited to 0.5 amps. Besides this detail, this layout was basically copied from the datasheet.


# System status

This system was completed and ran successfully on the 2018 sub Leviathan. No major issues were experienced and further iterations will deal with improving design rather than overhauling the board.

# Known Issues

- Schematic designs are a mess.
- Schematics use big generic box components rather than descriptive component logos.
- Lacking 3D models on PCB layout.
- PCB layout had some incorrectly sized footprints that caused some tight clearances
- No power management for proper startup and shutdown of power lines.
- Recom 5V potentially unreliable and not used for anything.
- No current monitoring to ensure correct operation of sub.
- No voltage monitoring to ensure correct operation of sub.
- Reverse voltage protection only provided by Molex header.
- Not able to properly monitor circuit health or thermals.
- Voltage outputs not exact and worsened with PCB trace resistances.
- No PGOOD monitoring on 9,12,19V lines for voltage accuracy.
- Poor RSense and Inductor selection for current limiting and ripple on 9,12,19V lines.
- PCB layouts and schematics were duplicated by hand instead of utilizing Altium properly.
- Current sense resistors may not guarantee proper linearity of AD8217 outputs.
- Maximum efficiency was not prioritized.

# Appendix

LTC3780: http://www.analog.com/en/products/power-management/switching-regulators/buck-boost-regulators/external-power-switch-buck-boost/ltc3780.html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

LT3958: http://www.analog.com/en/products/power-management/switching-regulators/flyback-forward-isolated-controllers/lt3958.html

MicroFit Molex Connector: https://www.molex.com/molex/products/datasheet.jsp?part=active/0447640801_PCB_RECEPTACLES.xml

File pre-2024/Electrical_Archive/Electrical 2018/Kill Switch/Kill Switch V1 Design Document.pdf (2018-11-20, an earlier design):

CU Robosub team

8/29/2018

# Kill Switch/ESC Board

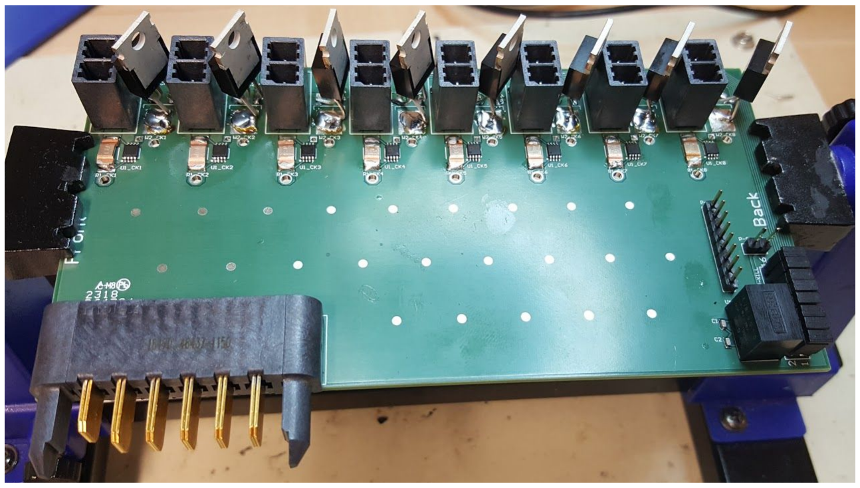
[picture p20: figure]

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
Kill S

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
# Abstract

The kill switch board controls all power to the ESC modules and therefore the motors. This board can cut the power to the motors based off the kill switch’s state, allowing voltage to pass through the onboard mosfets to ground or holding the voltage high so the motors have nothing to work off of.

# Design Requirements

The kill switch board must:
- Receive input power and ground connections from the backplane.
- Route proper connections for power and ground to every ESC module.
- Use the kill switch’s state to properly turn off the motors.
- Not overheat from the amount of current passing through it.

# Design Overview

All of the ESC modules are controlled by N-channel mosfets that had their gate connected to a 5V line which could be broken by the kill switch. The mosfet’s controlled the motor’s connection to ground, so if the kill switch was active, then the motors would float at 14.8V with no way to draw current and turn. When the kill switch was disabled, the 5V line would activate the mosfets which allowed the motors to create a complete circuit and rotate as desired by the Pololu controller.

## Previous designs

Previously, this board was combined with the merge board due to the power requirements of the motors and the sub. The previous design was functional, but there was too much power on that pcb, without proper thermal considerations, so it started melting off soldered components. The mosfets also were not reliable and several broke from various incidents of polarity and misuse.

# System descriptions

Shown below is the completed kill switch board design. Red represents top layer traces while blue represents bottom level traces. This board ended up being a four layer PCB in order to route power and ground planes more efficiently and to potentially improve thermals with extra copper pours.

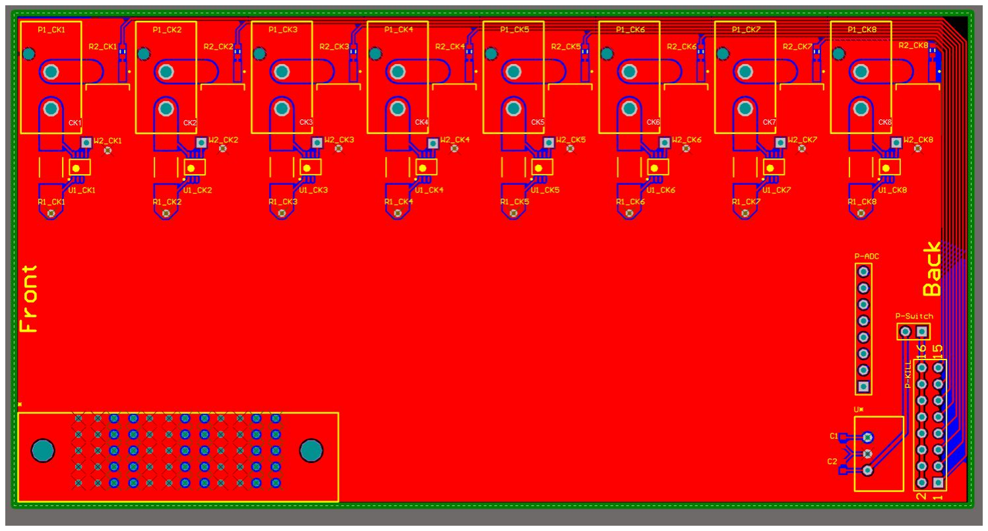
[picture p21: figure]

The top two layers of this board were reserved for the ground plane so that the mosfets could easily connect to the plane and pass as much current to it as needed. These planes were connected through a lattice of vias, not shown in the picture, to assure proper connections and thermal availability. The bottom two layers were set as the power plane that connected to the through-hole molex connectors. These connectors were for the ESC’s to connect to in a polarized way that couldn’t reverse polarity on accident like the previous bullet connectors. These bottom two planes were connected by more latticed vias to assure proper power distribution throughout the board. AD8217s were used as current monitors for the ESC inputs.

## Recom and Kill Switch

In the bottom right corner of this board a recom 5V converter was provided to create a gate signal for all of the mosfets. This voltage line immediately connected to the kill switch so that we could control the gate signals. The kill switch was soldered between the two horizontal vias labeled as p-switch. From the other end of the killswitch we created a row of jumper headers to connect all of the gates to the signal in an easy way. Due to the Recom’s max current specs and good electrical practices, we also implemented 1KOhm resistors in series in front of the gates to not kill the mosfets if any power spikes did occur for any reason.

# System status

This system was completed and ran successfully on the 2018 sub Leviathan. No major issues were experienced after soldering.

# Known Issues

- This board is potentially not needed. Due to the Pololu Motor Controller’s reset pin, we can cut all motors without this board. Resetting the Pololu will remove all data inputs for the ESC’s and they will stop providing power to the motors.
- Wrong mosfet connections. Flip source and drain routing for proper function
- Schematics only show boxes for the mosfets instead of their internal design. (This created the wrong mosfet orientation problem)
- Forgotten pulldown resistor from mosfet gates to GND
- Kill Switch soldering vias were easily stripped/deplated. Switch to Molex connectors

# Appendix

N-Channel Mosfets:
https://www.digikey.com/product-detail/en/infineon-technologies/IRLR6225TRPBF/IRLR6225TRPBFCT-ND/2538170 (https://www.digikey.com/product-detail/en/infineon-technologies/IRLR6225TRPBF/IRLR6225TRPBFCT-ND/2538170)
5V converter:
https://www.digikey.com/product-detail/en/recom-power/R-78E5.0-0.5/945-1648-5-ND/2834904 ESC Connectors:
https://www.molex.com/molex/products/datasheet.jsp?part=active/0768290102_PCB_HEADER S.xml (https://www.molex.com/molex/products/datasheet.jsp?part=active/0768290102_PCB_HEADERS.xml)

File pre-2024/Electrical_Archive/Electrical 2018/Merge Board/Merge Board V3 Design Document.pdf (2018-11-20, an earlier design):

CU Robosub team

9/1/2018

# Merge Board

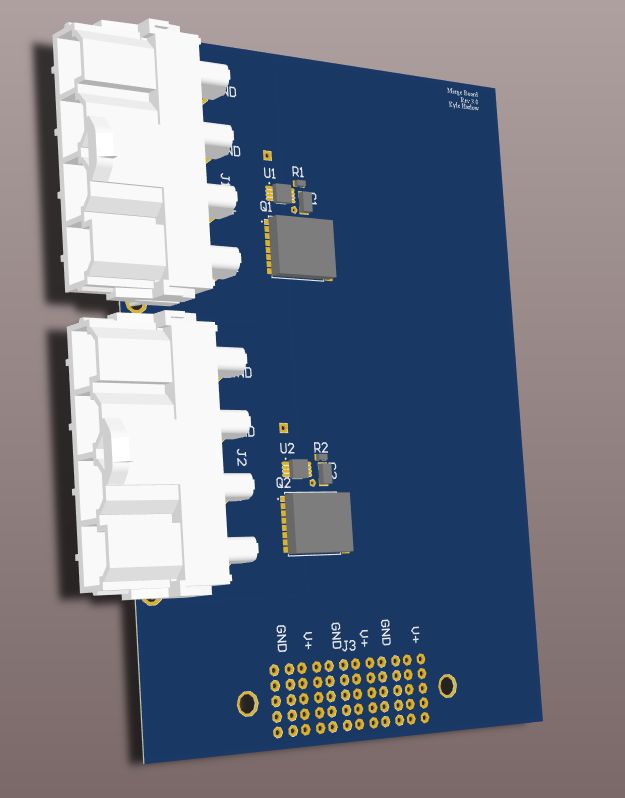
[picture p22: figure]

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
# Abstract

The merge board controls all input power to the sub from the two batteries. This board also balances the battery draw so that they drain equally and don’t start charging each other or dropping too quickly into dangerous low voltage states.

# Design Requirements

The merge board must:
- Receive input power and ground connections from the battery pods.
- Route proper connections for power and ground to the backplane.
- Not overheat from the amount of current passing through it.

# Design Overview

The batteries connect to the merge board through Molex CONNECTORS that can handle the large amount of current flowing through them. From there, the batteries are funnelled through high power mosfets from Infineon Technologies that can be turned off by commands from LTC4357s. The two LTC4357s perform OR operations to use the battery with the highest voltage, so that the sub will drain the fullest battery first. From there, the two battery inputs are merged into a 3oz copper plane and connected to the backplane for the other systems to use.

## Previous designs

Old merge boards used to combine both the kill switch/esc board and the merge board. This was to save space and cost, but due to oversights in copper thickness and design, these boards did not work as intended. Old desings had too small of copper necks from the battery connectors to the high power mosfets, so they would significantly heat up and potentially melt components off of the board. The old designs also used unreliable connectors to attach the battery leads which created worries for shorting and current throughput.

# System descriptions

Shown below is the completed kill switch board design. Red represents top layer traces while blue represents bottom level traces. This board ended up being a two layer PCB with 3oz copper pours in order to route power and ground planes more efficiently and to significantly improve thermals. While it would have been better, 6oz copper was not used due to the clearances the LTC4357 and mosfet’s pads need to work properly. To compensate for this, large power and ground planes were used to dissipate the extra heat.

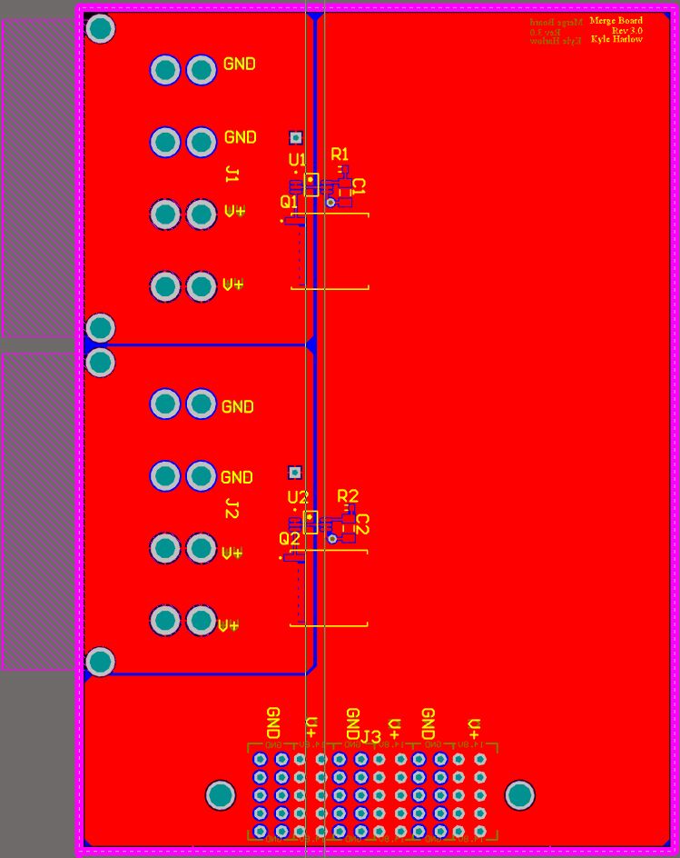
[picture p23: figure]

# System status

This system was completed and ran successfully on the 2018 sub Leviathan. No major issues were experienced after soldering.

# Known Issues

- This board is too tall. With the electrical rack, the clearance from this board to the acrylic tube is small enough to cause issues when taking the sub apart.
- The connector to the backplane cannot support the board completely and will get looser overtime.

# Appendix

Input Mosfets: https://www.digikey.com/products/en?keywords=IPT004N03LATMA1CT-ND LTC4357: https://www.digikey.com/products/en?keywords=LTC4357CMS8%23PBF-ND MiniFit Sr. Headers:
https://www.molex.com/molex/products/datasheet.jsp?part=active/0428204214_PCB_HEADER S.xml (https://www.molex.com/molex/products/datasheet.jsp?part=active/0428204214_PCB_HEADERS.xml)

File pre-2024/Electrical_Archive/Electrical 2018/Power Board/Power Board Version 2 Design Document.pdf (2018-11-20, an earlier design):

CU RoboSub Team
8/8/2018
Power Board V2

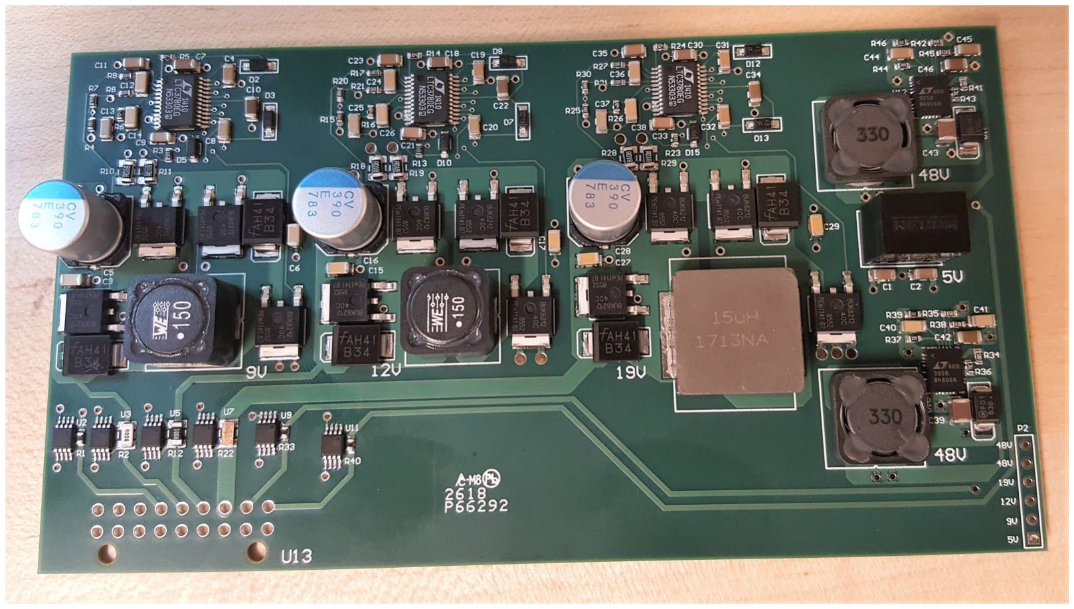
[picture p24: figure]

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
V lin

e

5
9

V lin

e

6
1

2

V lin

e

7
1

9

V lin

e

8
4

8

V lin

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
# Abstract

The power conversion board takes in approximately 14.8V from the merge circuit board through the backplane and converts it into various voltage levels to power each of the other electrical systems on the UAV.

# Design Requirements

Description | Specifications
5V line | 1A buck - Backup Line for Various Systems
9V line | 1A buck - Network Switch
12V line | 3A buck - Hydrophones, Pneumatic Systems, and Pressure Sensor
19V line | 4A boost - Computer
48V line | .5A boost - Down Camera with POE Injector
48V line 2 | .5A boost - DVL Power with ethernet splitting

# Design Overview

This board went through several revisions before this version was published. The revisions mostly involved reconfiguring layouts of the 9,12, and 19V lines along with redesigns to follow good PCB routing practices. These voltage lines used the LTC3780 controller with the recommended array of passive and active components. The two 48V lines used the recommended configurations for the LTC3958. These recommended designs can be found in the respective data sheets on Linear Technology’s website linked in the appendix.

## Previous designs

Design V1.0 was not of sufficient quality. It had no reverse bias protection which caused it to fail when brought to competition, along with several thermal, efficiency, and consistency issues. However, the buck and boost converters had quality designs and were continued into the second revision. Despite the good designs, the 19V line could not power a new computer, primarily due to components that could not handle the full 4A and incorrect current limiting resistors. The sub’s computer is a major component of the system so this board had to be redesigned for proper operation of the AUV.

# System descriptions


Shown below is the completed power board design. Red represents top layer traces while blue represents bottom level traces. This board ended up being a four layer PCB in order to route power and ground planes more efficiently and to potentially improve thermals with extra copper pours. The power plane is represented by the yellow plane and the ground is the cyan plane that covers the entire board. Each subsystem will be described in full within the subsequent sections.

## 5V line

This systems consists of taking a R-78E-0.5 low cost switching regulator and adding a few decoupling capacitors to the input and output lines. Followed by a current sensing resistor with a AD8217 Analog Devices high resolution, zero drift current shunt monitor chip. This device utilizes a 10 mOhm sense resistor to measure current draw as linear voltage based on the current drop across the sense resistor.


## 9V line

This systems consists of taking the LT3780’s recommended schematic, adding a few decoupling capacitors, and changing the Vosense resistors. The implemented Vosense resistors of 113kOhm and 11kOhm provide an output voltage of 9.02V. Reading the datasheet will be required for complete understanding of this IC. In brief, the voltage is modulated with an inductor and passed through external mosfets controlled by the IC’s oscillation cycles to allow for a variety of power requirements. This is all followed by a current sensing resistor with a AD8217. This device utilizes a 6mOhm sense resistor to measure current draw as linear voltage based on the current drop across the sense resistor.
The PCB layout of this circuit also follows the recommended design from the LT3780’s data sheet for optimal efficiency and ease of design. Due to the high current passing through some of the components, the component pad to polygon neck widths were increased from default, larger/duplicated vias were used to provide safe and sufficient power management, and output trace widths to the connector were increased based on online thermal and resistance calculators for PCB traces.


## 12V line

This systems consists of taking the LT3780’s recommended schematic, adding a few decoupling capacitors, and changing the Vosense resistors. The implemented Vosense resistors of 113kOhm and 8.06kOhm provide an output voltage of 12.02V. This line utilizes a 3mOhm sense resistor for its AD8217 to measure current draw as linear voltage based on the current drop across the sense resistor. The PCB layout of this circuit also follows the recommended design from the LT3780’s data sheet for optimal efficiency and ease of design. For further questions refer to the 9V line for a summary of this system since they are identical.


## 19V line

This systems consists of taking the LT3780’s recommended schematic, adding a few decoupling capacitors, and changing the Vosense resistors. The implemented Vosense resistors of 113kOhm and 4.99kOhm provide an output voltage of 18.92V. This device utilizes a 1mOhm sense resistor for its AD8217 to measure current draw as linear voltage based on the current drop across the sense resistor. The PCB layout of this circuit also follows the recommended design from the LT3780’s data sheet for optimal efficiency and ease of design. For further questions, refer to the 9V line for a summary of this system since they are identical besides the boost conversion.


## 48V line

This systems consists of taking the LT3958’s recommended 48V schematic and adding a few decoupling capacitors. Reading the datasheet will be required for complete understanding of this IC. In brief, the voltage is modulated with an inductor and feedback loops through internal regulators, comparators, and a variety of oscillation cycles. This is all followed by a current sensing resistor with a AD8217. This device utilizes a 10 mOhm sense resistor to measure current draw as linear voltage based on the current drop across the sense resistor.
The PCB layout for this system is fully detailed with pictures in the LT3958’s data sheet, so implementation is fairly straightforward. We implemented multiple polygon pours that had no thermal relief/component pad to polygon necks due to the tight clearances of the LT3958 and the system being limited to 0.5 amps. Besides this detail, this layout was basically copied from the datasheet.


# System status

This system was completed and ran successfully on the 2018 sub Leviathan. No major issues were experienced and further iterations will deal with improving design rather than overhauling the board.

# Known Issues

- Schematic designs are a mess.
- Schematics use big generic box components rather than descriptive component logos.
- Lacking 3D models on PCB layout.
- PCB layout had some incorrectly sized footprints that caused some tight clearances
- No power management for proper startup and shutdown of power lines.
- Recom 5V potentially unreliable and not used for anything.
- No current monitoring to ensure correct operation of sub.
- No voltage monitoring to ensure correct operation of sub.
- Reverse voltage protection only provided by Molex header.
- Not able to properly monitor circuit health or thermals.
- Voltage outputs not exact and worsened with PCB trace resistances.
- No PGOOD monitoring on 9,12,19V lines for voltage accuracy.
- Poor RSense and Inductor selection for current limiting and ripple on 9,12,19V lines.
- PCB layouts and schematics were duplicated by hand instead of utilizing Altium properly.
- Current sense resistors may not guarantee proper linearity of AD8217 outputs.
- Maximum efficiency was not prioritized.

# Appendix

LTC3780:
http://www.analog.com/en/products/power-management/switching-regulators/buck-boost-regulators/external-power-switch-buck-boost/ltc3780.html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 (http://www.analog.com/en/products/power-management/switching-regulators/buck-boost-regulators/external-power-switch-buck-boost/ltc3780.html)

LT3958:
http://www.analog.com/en/products/power-management/switching-regulators/flyback-forward-isolated-controllers/lt3958.html (http://www.analog.com/en/products/power-management/switching-regulators/flyback-forward-isolated-controllers/lt3958.html)

MicroFit Molex Connector:
https://www.molex.com/molex/products/datasheet.jsp?part=active/0447640801_PCB_RECEPT ACLES.xml (https://www.molex.com/molex/products/datasheet.jsp?part=active/0447640801_PCB_RECEPTACLES.xml)

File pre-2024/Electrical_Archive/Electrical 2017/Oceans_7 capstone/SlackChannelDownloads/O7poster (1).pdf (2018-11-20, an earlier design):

# Ocean’s Seven

Hasan Alahmed, Abbigail Caballero, Kyle Harlow, Daniel Henderson,

# Yuvin Kokuhennadige, Cassandra Noice

# Power Requirements

### - Receives a 14.8V line from the backplane - Must deliver five different power outputs to the backplane

# Controls Requirements

### - Pitch, Roll, and Yaw - Velocity - Depth

# Plant Analysis

- Drag makes system non-linear, therefore harder to develop a controller
- Linearize Plant around specific operating points thetadot
- Develop controllers individually and use gain scheduling

# Controller Design

- Stability concerns for θ̇
≈ 0
- Drag: acts as a differential term
- Integrator: unfeasible
• Third pole at ω = 0 rad/s destabilizes system when θ̇
≈ 0
| rad/s
| • PM ≈ -90 degrees

# Software

- Makes use of the
STMicroelectronics HAL (Hardware Abstraction Layer) libraries
- Implements UART communication, 8 simultaneous PWM signals
- Performs controls algorithms as data is received, ~10-20 Hz

# Hardware

- Custom PCB
- STM32F767Z1 ARM M7
microcontroller
- FT232 UART/USB converter to communicate with robosub main PC
- Power conversion: 5V to 3.3V
- JTAG programming interface

# Merge Board

- Current controlled positive high voltage ideal diode controller (Current merge circuit) to get a 200A output from two 100A batteries at 14.8V
- 14.8V, 140A output for motors through kill switch to turn off the motors for safety
- Current sensing using current shunt monitors and Arduino Micro
- 5V with maximum current draw of 1A for digital components
- 12V with maximum current draw of 3A for electromechanical actuators
- 19V with maximum current draw of 4A for main computer
- 48V with maximum current draw of 0.5A for Doppler Velocity Logger (DVL)
- 48V with maximum current draw of 0.5A for a camera through Power over Ethernet (PoE)
- Current sensing using current shunt monitors and Arduino Micro
- Gain Scheduled Lead Lag
Compensator
| • Boost phase margin at ω ≈ 10 rad/s
| • Boost gain margin
- Provide connectivity and stability to merge board, ESC holders, control board and power conversion board
- Takes in 14.8V at 40A from current merge circuit
- Delivers 5V, 12V, 19V,
and 48V from the power
conversion board to the
controls system, CPU, and
sensors
- Provide PWM from the
controls system to ESCs

# Success Criteria

### - Settle Time: 5 seconds - Overshoot: 10% - Reject Step Disturbance

# Power Board

# Backplane

# Controls Board

# RoboSub Background

### The University of Colorado – Boulder Robosub Team has been competing in the AUVSI Robosub

Competition for four years.

### For Robosub competition student teams from around the world build autonomous robotic submarines which compete in a rigorous underwater obstacle course, which simulates real

world tasks robots may be expected to perform.

# Sponsored by the CU Robotics Club Special thanks to Cristopher "Topher" Pollard and Jeff Venicx

# Power, Backplane & Controls System for Leviathan

ODE of Plant Dynamics

Final Controller Design

Bode Plot of plant dynamics for yaw controller linearized at θ̇
= 0, 0.2, 0.4, 0.6, 0.8

Closed loop step response of plant and controller
PCB layout for the Backplane

PCB layout for the Power board

PCB layout for the Merge board

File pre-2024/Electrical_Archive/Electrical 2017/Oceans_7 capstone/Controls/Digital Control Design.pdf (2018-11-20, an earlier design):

### Sampled-data control of nonlinear systems: an overview of recent results

Dragan Nešić¹ and Andrew R. Teel²

1 Department of Electrical and Electronic Engineering, The University of Melbourne, Parkville, 3010, Victoria, Australia
2 CCEC, Electrical and Computer Engineering Department, University of California, Santa Barbara, CA, 93106-9560

Abstract. Some recent results on design of controllers for nonlinear sampled-data systems are surveyed.

### 1 Introduction

The prevalence of digitally implemented controllers and the fact that the plant dynamics and/or the controller are often nonlinear strongly motivate the area of nonlinear sampled-data control systems. When designing a controller for a sampled-data nonlinear plant, one is usually faced with an important intrinsic difficulty: the exact discrete-time/sampled-data model of the plant can not be found.
The absence of a good model of a sampled-data nonlinear plant for a digital controller design has lead to several methods that use different types of approximate models for this purpose. We single out two such methods that attracted lots of attention in the sampled-data control literature and that consist of the following steps:
Method 1: | Method 2:
continuous-time plant model | continuous-time plant model
⇓ | ⇓
continuous-time controller | discretize plant model
⇓ | ⇓
discretize controller | discrete-time controller
⇓ | ⇓
implement the controller | implement the controller

Hence, in Method 1 (this method is often referred to as the controller emulation design) one first designs a continuous-time controller based on a continuous-time plant model. At this step the sampling is completely ignored. Then, the obtained continuous-time controller is discretized and implemented using a sampler and hold device. On the other hand, in Method 2 one first

2 | D. Nešić and A.R. Teel

finds a discrete-time model of the plant, then designs a discrete-time controller based on this discrete-time model and finally implements the designed discrete-time controller using a sampler and hold device.
In principle, Method 2 is more straightforward for linear systems than for nonlinear systems. Indeed, for linear systems we can write down an explicit, exact discrete-time model while typically for nonlinear systems we cannot. Moreover, the exact discrete-time model of a linear system is linear while the exact discrete-time model for a sampled-data nonlinear system does not usually preserve important structures of the underlying continuous-time nonlinear system, like affine controls for example. Consequently, for nonlinear systems it is unusual to assume knowledge of the exact discrete-time model of the plant whereas this assumption is made in most of classical linear literature. However, often due to our inability to exactly compute the matrix exponential that generates the exact discrete-time model of a linear plant, we use its approximation and hence we actually use an approximate discrete-time plant model for controller design most of the time, even for linear systems. Consequently, we will always assume in the sequel that in Method 2 we use an approximate discrete-time model of the plant for controller design.
The main question in Method 1 is whether the desired properties of the continuous-time closed loop system that the designed controller yielded will be preserved and, if so, in what sense for the closed-loop sampled-data system. Similarly, the central question in Method 2 is whether or not the properties of the closed-loop system consisting of the exact discrete-time plant model and the discrete-time controller will have similar properties as the closed-loop system consisting of the approximate discrete-time plant model and the discrete-time controller. In this paper, we present some answers to these questions for both methods. In particular, we overview several recent results on Methods 1 and 2 for general nonlinear plants that appeared in [21,27– 31,41]. These results do not contain algorithms for controller design. In the case of Method 1, controller design is the topic of the area of continuous-time nonlinear control. In the case of Method 2, controller design algorithms are yet to be developed and our results provide a unified framework for doing this.
The paper is organized as follows. In Section 2 we present results on Method 1 and in Section 3 we present results on Method 3. We do not present any proofs and the reader may refer to original references for proofs of all results.

### 2 Method 1: Emulation

Many results for nonlinear sampled-data systems uses controller emulation because of the simplicity of the method and the fact that a wide range of continuous-time controller design methods can be directly used for design of digital controllers, see [3,33,34,42,41]. An important drawback of the exist-

Sampled-data control of nonlinear systems | 3

ing nonlinear sampled-data theory is that only the questions of stability (see [3,33,34,42]) and input-to-state stability (see [41]) were addressed within the emulation design framework. However, one may be interested in a range of other important system theoretic properties, such as passivity and Lp stability. It turns out that a rather general notion of dissipativity that we consider ((V, w)-dissipativity, see Definition 1) can be used to cover a range of most important system theoretic properties within a unified framework. Special cases of (V, w)-dissipativity are: stability, input-to-state stability, passivity, Lp stability, forward completeness, unboundedness observability, etc. Results in this section are taken from [30] and are concerned with preservation of (V, w)-dissipativity under sampling in the emulation design for the cases of static state feedback controllers and open loop controls. Results on emulation of dynamic state feedback controllers can be found in [21] and they are not presented here for space reasons. Hence, results in [21,30] provide a general and unified framework for digital controller design using Method 1.

### 2.1 Preliminaries

In order to state our results precisely, we need to state some definitions and assumptions. Sets of real and natural numbers are respectively denoted as R and N. The Euclidean norm of a vector x is denoted as |x|. Given a set B ⊂ R

n, its ² neighborhood is denoted as N(B, ²) := {x : infz∈B |x − z| ≤ ²}. A function γ : R≥0 → R≥0 is of class-N if it is continuous and non-decreasing. It is of class-K if it is continuous, zero at zero and strictly increasing; it is of class-K∞ if it is of class-K and is unbounded. A continuous function β : R≥0 ×R≥0 → R≥0 is of class-KL if β(·, τ ) is of class-K for each τ ≥ 0 and β(s, ·) is decreasing to zero for each s > 0. For a given function d(·), we use the following notation d[t1, t2] := {d(t) : t ∈ [t1, t2]}. If t1 = kT, t2 = (k+ 1)T, we use the shorter notation d[k], and take the norm of d[k] to be the supremum of d(·) over [kT,(k + 1)T], that is

kd[k]k∞ = ess sup

τ∈[kT ,(k+1)T]

|d(τ )| .

Consider the continuous-time nonlinear plant:

x˙ = f(x, u, dc, ds), | (1)
y = h(x, u, dc, ds), | (2)

where x ∈ R

n, u ∈ R

m and y ∈ R

p are respectively the state, control input and the output of the system and dc ∈ R

nc and ds ∈ R

ns are disturbance inputs to the system. It is assumed that f and h are locally Lipschitz, f(0, 0, 0, 0) = 0 and h(0, 0, 0, 0) = 0.
A starting point in the emulation design is to assume that a continuous-time (open-loop or closed loop system with an appropriately designed continuous-time controller) possesses a certain property, such as stability. We will assume

4 | D. Nešić and A.R. Teel

in the sequel that the continuous system satisfies the following dissipation property:

Definition 1. The system (1), (2) is said to be (V, w)-dissipative if there exist a continuously differentiable function V , called the storage function, and a continuous function w : R

n × R

m × R

nc × R

ns → R, called the dissipation rate, such that for all x ∈ R

n, u ∈ R

m, dc ∈ R

nc
, ds ∈ R

ns the following holds:

∂V
∂x f(x, u, dc, ds) ≤ w(x, u, dc, ds). | (3)

¥

(V, w)-dissipation is a rather general property whose special cases are stability, input-to-state stability, passivity, etc.
Besides the continuous-time model (1), (2), we consider the exact discrete-time model for (1), (2) when some of the variables in function f of (1), (2) are sampled or assumed piecewise constant. More precisely, let T > 0 be a sampling period and suppose that u and ds in f in (1) are constant during the sampling intervals, so that u(t) = u(kT) =: u(k) and ds(t) = ds(kT) =: ds(k), ∀t ∈ [kT,(k+1)T), ∀k ≥ 0, and y is measured only at sampling instants kT, k ≥ 0.
The exact discrete-time model for the system (1), (2) is obtained by integrating the initial value problem
x˙(t) = f(x(t), u(k), dc(t), ds(k)), | (4)

with given ds(k), dc[k], u(k) and x0 = x(k), over the sampling interval [kT,(k + 1)T]. Let x(t) denotes the solution of the initial value problem (4) with given ds(k), dc[k], u(k) and x0 = x(k). Then, we can write the exact discrete-time model for (1), (2) as:

x(k + 1) = x(k) + Z (k+1)T

kT

f(x(τ ), u(k), dc(τ ), ds(k))dτ

:= F

e
T
(x(k), u(k), dc[k], ds(k)) , | (5)
y(k) = h(x(k), u(k), dc(k), ds(k)) . | (6)

The sampling period T is assumed to be a design parameter which can be arbitrarily assigned. In practice, the sampling period T is fixed and our results could be used to determine if it is suitably small. We emphasize that F

e
| T in
(5) is not known in most cases. We denote dc := dc(0) and use it in the sequel.

### 2.2 Main results

We now present a series of results which provide a general framework for the emulation design method. In Theorems 1 and 2 we respectively consider the

Sampled-data control of nonlinear systems | 5

“weak” and the “strong” dissipation inequalities for the exact discrete-time model of the sampled-data system. Each of these dissipation inequalities is useful in certain situations, as illustrated in the last subsection, where they are applied to problems of input-to-state stability and passivity. Then several corollaries are stated for the closed-loop system consisting of (1), (2) and different kinds of static state feedback controllers. Examples are presented to illustrate different conditions in main results. For simplicity we do not present results on emulation of dynamic feedback controllers and these results can be found in [21].

Theorem 1. (Weak form of dissipation) If the system (1), (2) is (V, w)-dissipative, then given any 6-tuple of strictly positive real numbers
(∆x, ∆u, ∆dc
, ∆d˙
c

, ∆ds

, ν), there exists T

∗ > 0 such that for all T ∈ (0, T ∗ )
and all |x| ≤ ∆x, |u| ≤ ∆u, |ds| ≤ ∆ds and functions dc(t) that are Lipschitz and satisfy kdc[0]k∞ ≤ ∆dc and

°
°
°

ḋc[0]

°
°
°
∞

≤ ∆d˙

c

, the following holds for the exact discrete-time model (5) of the system (1), (2):

∆V
T

:=

V (F

e
T

(x, u, dc[0], ds)) − V (x) T

≤ w(x, u, dc, ds) + ν . | (7)

¥

Under slightly stronger conditions we can prove a stronger result that is useful in some situations:

Lemma 1. If the system (1), (2) is (V, w)-dissipative, with ∂V
∂x being locally
Lipschitz and ∂V
∂x (0) = 0, then given any quintuple of strictly positive real numbers (∆x, ∆u, ∆dc

, ∆d˙

c

, ∆ds

), there exist T

∗ > 0 and positive constants K1, K2, K3, K4, K5 such that for all T ∈ (0, T ∗
) and all |x| ≤ ∆x, |u| ≤ ∆u, |ds| ≤ ∆ds and functions dc(t) that are Lipschitz and satisfy kdc[0]k∞ ≤ ∆dc

, °
°
°

ḋc[0]

°
°
°
∞

≤ ∆d˙

c

, we have:

∆V
T

≤ w(x, u, dc, ds) +

T

µ
K1|x|

2 + K2|u|

2 + K3|ds|

2 + K4 kdc[0]k

2
∞ + K5

°
°
°

ḋc[0]

°
°
°

2

∞

¶
. (8)

¥
In the following theorem we use the strong form of dissipation inequality for the exact discrete-time model. This result is much more natural to use in the situations when the disturbances dc are not globally Lipschitz (see the ISS application in the next subsection and Example 1).

Theorem 2. (Strong form of dissipation) If the system (1), (2) is (V, w)-dissipative, then given any quintuple of strictly positive real numbers

6 | D. Nešić and A.R. Teel

(∆x, ∆u, ∆dc
, ∆ds

, ν) there exists T

∗ > 0 such that for all T ∈ (0, T ∗ ) and all
|x| ≤ ∆x, |u| ≤ ∆u, kdc[0]k∞ ≤ ∆dc

, and |ds| ≤ ∆ds

the following holds for
the system (5):

∆V
T

≤

1
T

Z T

0

w(x, u, dc(τ ), ds)dτ + ν . | (9)
| ¥
It is very important to state and prove Theorems 1 and 2 for the case when a feedback controller is used to achieve (V, w)-dissipativity of the closed loop system. To prove result on weak dissipation inequalities, we consider the situation when static state feedback controller of the form:
u = u(x, dc, ds) | (10)

is applied to the system (1), (2). It is assumed below that the feedback (10) is bounded on compact sets. Note that this general form of feedback covers both, the full state (u = u(x)) and output (u = u(y)) static feedback. Note also, that the dissipation rate for the closed-loop system (1), (2) and (10) in the definition of (V, w)-dissipativity can be taken as w = w(x, dc, ds). Direct consequences of Theorem 1 and Lemma 1 are the following corollaries: Corollary 1. If the system (1), (2), (10) is (V, w)-dissipative, then given any quintuple of strictly positive real numbers (∆x, ∆dc
, ∆d˙
c

, ∆ds

, ν), there
exists T

∗ > 0 such that for all T ∈ (0, T ∗
) and all |x| ≤ ∆x, |ds| ≤ ∆ds and all functions dc(t) that are Lipschitz and satisfy kdc[0]k∞ ≤ ∆dc

,

°
°
°

ḋc[0]

°
°
°
| ∞ ≤

∆d˙
c

, the following holds for the discrete-time model of the closed-loop system (1), (2), (10):

∆V
T
≤ w(x, dc, ds) + ν . | (11)
| ¥
Corollary 2. If the system (1), (2), (10) is (V, w)-dissipative, with ∂V
∂x and
u(x, dc, ds) in (10) being locally Lipschitz and ∂V
∂x (0) = 0 and u(0, 0, 0) = 0, then given any quadruple of strictly positive real numbers (∆x, ∆dc , ∆d˙
c
| , ∆ds

),
there exists T

∗ > 0 and positive constants K1, K2, K3, K4 such that for all T ∈ (0, T ∗
) and all |x| ≤ ∆x, |ds| ≤ ∆ds and functions dc(t) that are Lipschitz and satisfy kdc[0]k∞ ≤ ∆dc and

°
°
°

ḋc[0]

°
°
°
∞

≤ ∆d˙

c

, the closed-loop discrete-time model for system (1), (2) and (10) satisfies:

∆V
T

≤ w(x, dc, ds) +

T

µ
K1|x|

2 + K2|ds|

2 + K3 kdc[0]k

2
∞ + K4

°
°
°

ḋc[0]

°
°
°

2

∞

¶
| ¥

Sampled-data control of nonlinear systems | 7

It is interesting to note that the condition on the derivative dc in Theorem 1 is necessary to prove the weak dissipation inequality for the discrete-time system. The following example illustrates this.

Example 1. Consider the continuous time system:

x˙ = u(x) + dc = −x + dc, | (12)

where x, dc ∈ R. Using the storage function V =
1/2 x

2
, the derivative of V
is V˙ = −x
2 + xdc ≤ −¹
2

x

2 +
1/2 d

2
c

, and (12) is ISS. We will show that if dc(t) = cos ¡
t+2T
T

¢
the claim of Theorem 1 does not hold since
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
sin µ
t + 2T
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
, | (13)

which goes to infinity as T → 0. Assume that u(x) in (12) is piecewise constant for the sampled-data system. So, the discrete-time model of the sampled-data system is

x(k + 1) = (1 − T)x(k) + Z (k+1)T

kT

cos µ
τ + 2T
T

¶
dτ , (14)

and hence the exact discrete-time model is given by:

x(k + 1) = (1 − T)x(k) + T [sin(k + 3) − sin(k + 2)] , ∀k ≥ 0. (15)

Suppose that for any given ∆x, ∆dc

and ν, there exists T

∗ > 0 such that for
all T ∈ (0, T ∗
) and k ≥ 0 with |x| ≤ ∆x and kdc[0]k∞ ≤ ∆dc we have

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
c + ν. | (16)

We show by contradiction that the claim is not true for our case. Direct computations yield:

∆V
T

=

((1 − T)x + T [sin(3) − sin(2)])² − x
2
2T
= −x
2 + x [sin(3) − sin(2)] + O(T). | (17)

Let ˜x = −0.5, (and hence ∆x = 0.5, ∆dc = 1). By combining (16) and (17) we conclude that there should exist T

∗ > 0 such that ∀T ∈ (0, T ∗ ) we obtain:

−

1
2

x˜

2 + ˜x [sin(3) − sin(2)] −

1
2

cos(2)² − ν + O(T) ≤ 0 , (18)

and since there exists ν

∗ > 0 such that −
1/2 x˜

2+ ˜x [sin(3) − sin(2)]−

1/2 cos(2)² =
ν

∗ we can rewrite (18) as ν

∗−ν +O(T) ≤ 0 , which is a contradiction (it does

8 | D. Nešić and A.R. Teel

not hold for ν ∈ (0, ν∗

)). Therefore, for ∆x = 0.5, ∆dc = 1, ν < ν∗ , there
exists no T

∗ > 0, such that ∀T ∈ (0, T ∗ ) the condition (16) holds. Note that the chosen dc(t) does not satisfy the condition

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
≤ ∆d˙

c

for some fixed

∆d˙
c

> 0, which is evident from (13). Hence, in this case we can not apply
Theorem 1. | N

To state results on strong dissipation inequalities with static state feedback controllers, we need to consider controllers of the following form:

u = u(x, ds) , | (19)

in order to be able to state a general results on strong dissipation inequalities. This is illustrated by the following example.

Example 2. Consider the system ẋ = u, and u = −dc, where dc(0) = 0 and dc(t) = 1, ∀t > 0. Using V (x) = x, such that ∂V
∂x (−dc) = −dc and
w(x, dc, ds) = −dc. Since u is sampled and dc(0) = 0, we have that x(t) = 0, ∀t ∈ [0, T] and so ∆V /T = 0. On the other hand R T
0 w(dc(τ ))dτ = −T.
Hence, if (20) was true, then we would obtain obtain 0 ≤ −1 + ν, which is
not true for small ν. | ¥

Corollary 3. If the system (1), (2), (19) is (V, w)-dissipative, then given any quadruple of strictly positive real numbers (∆x, ∆dc
, ∆ds

, ν), there exists
T

∗ > 0 such that for all T ∈ (0, T ∗ ) and all |x| ≤ ∆x, kdc[0]k∞ ≤ ∆dc

, and
|ds| ≤ ∆ds

the following holds for the closed-loop discrete-time model of the system (1), (2) and (19):

∆V
T

≤

1
T

Z T

0

w(x, dc(τ ), ds)dτ + ν . | (20)

¥

Corollary 4. If the system (1), (2), (19) is (V, w)-dissipative, with ∂V ∂x and
u(x, ds) in (19) being locally Lipschitz and ∂V
∂x (0) = 0, u(0, 0) = 0, then given any triple of strictly positive real numbers (∆x, ∆dc , ∆ds

), there exists
T

∗ > 0 and positive constants K1, K2, K3 such that for all T ∈ (0, T ∗ ) and
all |x| ≤ ∆x, kdc[0]k∞ ≤ ∆dc

, and |ds| ≤ ∆ds

the closed-loop discrete-time model for the system (1), (2) and (19) satisfies:

∆V
T

≤

1
T

Z T

0

w(x, dc(τ ), ds)dτ + T

³
K1|x|

2 + K2|ds|

2 + K3 kdc[0]k

2
∞

´

¥

| Sampled-data control of nonlinear systems | 9

### 2.3 Applications

The weak and strong discrete-time dissipation inequalities in Theorems 1 and 2 are tools that can be used to show that the trajectories of the sampled-data system with an emulated controller have a certain property. In order to illustrate what kind of properties can be proved for the sampled-data system using the weak or strong inequalities, we apply our results to two important system properties: input-to-state stability and passivity. The results on input-to-state stability were proved in [30] and in [31]. The sketch of proof of the result on passivity can be found in [30]. Further applications of weak and strong inequalities to investigation of Lp stability, integral ISS, etc. are possible and are interesting topics for further research.

Input-to-state stability: Let us suppose that the system
x˙(t) = ˜f(x(t), u(t), dc(t)) | | (21)

can be rendered ISS using the locally Lipschitz static state feedback

u = u(x), | | (22)

in the following sense:
Definition 2. The system ẋ = f(x, dc) is input-to-state stable if there exists β ∈ KL and γ ∈ K such that the solutions of the system satisfy |x(t)| ≤
β(|x(0)| , t) + γ(kdck∞), ∀x(0), dc ∈ L∞, ∀t ≥ 0 . | ¥
Suppose also that the feedback needs to be implemented using a sampler and zero order hold, that is:
u(t) = u(x(k)) | t ∈ [kT,(k + 1)T), k ≥ 0 | (23)

The following result was first proved in [41] and an alternative proof was presented in [30]. The proof in [30] is based on the result on strong dissipation inequalities given in Corollary 3 and the results in [27]. In this case, the results on weak dissipation inequalities could not be used. This is because we do not want to impose the condition that the disturbances are Lipschitz when proving the following result, and that is a standing assumption in results on weak dissipation inequalities.

Corollary 5. If the continuous time system (21), (22) is ISS, then there exist β ∈ KL, γ ∈ K such that given any triple of strictly positive numbers (∆x, ∆dc

, ν), there exists T

∗ > 0 such that for all T ∈ (0, T ∗
| | ), |x(t0)| ≤ ∆x,
kdck∞ ≤ ∆dc

, the solutions of the sampled-data system (21), (23) satisfy:

|x(t)| ≤ β(|x(t0)|, t − t0) + γ(kdck∞) + ν, | (24)
∀t ≥ t0 ≥ 0. | | ¥

10 D. Nešić and A.R. Teel

Corollary 5 states that if the continuous-time closed loop system is ISS, then the sampled-data system with the emulated controller will be semiglobally practically ISS, where the sampling period is the parameter that we can adjust. Besides the above given property that is presented in an L∞ setting, we can prove the following integral (or L2) version of the same result that was proved in [31].

Corollary 6. If the system (21), (22) is ISS, then given any quadruple of strictly positive real numbers (∆x, ∆w, ν1, ν2) there exists T

∗ > 0 such that
for all T ∈ (0, T ∗
), |x(0)| ≤ ∆x and kwk∞ ≤ ∆w, the following inequality holds for the sampled-data system (21), (23) satisfy:
Z t

0

α3(|x(s)|)ds ≤ α2(|x(0)|) + Z t

0

γ(|w(s)|)ds + ν1t + ν2, | (25)
for all t ≥ 0. | ¥

Passivity: Consider the continuous time system with outputs

x˙ = f(x, u), y = h(x, u), | (26)

where x ∈ R

n, y, u ∈ R

m and assume that the system is passive, that is (V, w)-dissipative, where V : R

n → R≥0 and w = y

T u. We can apply either
results of Theorem 1 or 2 since u is a piecewise constant input, to obtain that the discrete-time model satisfies the following: for any (∆x, ∆u, ν) there exists T

∗ > 0 such that for all T ∈ (0, T ∗
), |x| ≤ ∆x, |u| ≤ ∆u we have:

∆V
T

≤ y

T u + ν. | (27)

In stability and ISS applications, adding ν in the dissipation inequality deteriorated the property, but the deterioration was gradual. However, in (27) ν acts as an infinite energy storage (finite power source) and hence it contradicts the definition of a passive system as one that can not generate power internally. As a result, conditions which guarantee that ν in (27) can be set to zero are very important. These conditions are spelled out in the next corollary:

Corollary 7. Suppose that the system (26) is strictly input and state passive in the following sense: the storage function has gradient ∂V
∂x that is locally
Lipschitz and zero at zero and the dissipation rate can be taken as w(x, y, u) = y

T u−ψ1(x)−ψ2(u), where ψ1 and ψ2 are positive definite functions that are locally quadratic. Then given any pair of strictly positive numbers (∆x, ∆u) there exists T

∗ > 0 such that for all T ∈ (0, T ∗ ), |x| ≤ ∆x, |u| ≤ ∆u we have:

∆V
T

≤ y

T u −

1
2

ψ1(x) −

1
2
ψ2(u). | (28)
| ¥

Sampled-data control of nonlinear systems 11

### 3 Method 2: Approximate discrete-time model design

As we already indicated in the introduction, a majority of nonlinear and linear discrete-time control literature is based on the assumption, which is unrealistic in general, that the exact discrete-time model of the plant is known. In reality, even in the case of linear systems we use an approximate discrete-time model for the discrete-time controller design. We recognize this fact and whenever we refer to Method 2, we always assume that only an approximate discrete-time model is available for the controller design.
One may be tempted to believe that if a controller is designed for an approximate discrete-time model of the plant with a sufficiently small sampling period then the same controller will stabilize the exact discrete-time model. Note that if this was true then one could directly apply all the existing theory that assumes that the exact discrete-time model is known. However, this reasoning is wrong since no matter how small the sampling period is, we may always find a controller that stabilizes the approximate model for that sampling period but destabilizes the exact model for the same sampling period, as illustrated by the following example.

Example 3. Consider the triple integrator ẋ1 = x2 , x˙ 2 = x3 , x˙ 3 = u, its Euler approximate model

x1(k + 1) = x1(k) + T x2(k)
x2(k + 1) = x2(k) + T x3(k) x3(k + 1) = x3(k) + T u(k) , | (29)

and a minimum-time dead-beat controller for the Euler discrete-time model given by
u(k) = µ
−

x1(k)
T³

−

3x2(k)
T²

−

3x3(k)
T

¶
. | (30)

The closed loop system consisting of (29) and (30) has all poles equal to zero for all T > 0 and hence this discrete-time Euler-based closed loop system is asymptotically stable for all T > 0. On the other hand, the closed loop system consisting of the exact discrete-time model of the triple integrator and controller (30) has a pole at ≈ −2.644 for all T > 0. Hence, the closed-loop sampled-data control system is unstable for all T > 0 (and, hence, also for arbitrarily small T)! So we see that, to design a stabilizing controller using Method 2, it is not sufficient to design a stabilizer for an approximate discrete-time model of the plant for sufficiently small T. Extra conditions are needed!

Several control laws in the literature have been designed based on approximate discrete-time models of the plant, see [8,12,23]. These results are always concerned with a particular plant model and a particular approximate discrete-time model (usually the Euler approximation) and hence they

12 D. Nešić and A.R. Teel

are not very general. On the other hand, we present a rather general result for a large class of plants, a large class of approximate discrete-time models and the conditions we obtain are readily checkable. For different approximate discretization procedures see [25,38,39,37].
Results in this section are based mainly on [28] and they address the design of stabilizing static state feedback controllers based on approximate discrete-time plant models. A more general result was recently proved in
[29] where conditions are presented for dynamic feedback controllers that are designed for approximate discrete-time models of sampled-data differential inclusions to prove stability with respect to arbitrary non-compact sets.

### 3.1 Main results

Consider the nonlinear continuous-time control system:

x˙ = f(x, u) | x(0) = x◦ | (31)

where x ∈ R

n, u ∈ R

m are respectively the state and control vectors. The function f is assumed to be such that, for each initial condition and each constant control, there exists a unique solution defined on some (perhaps bounded) interval of the form [0, τ ). The control is taken to be a piecewise constant signal u(t) = u(kT) =: u(k), ∀t ∈ [kT,(k + 1)T[, k ∈ N where T > 0 is a sampling period. We assume that the state measurements x(k) := x(kT) are available at sampling instants kT, k ∈ N. The sampling period T is assumed to be a design parameter which can be arbitrarily assigned (in practice, the sampling period T is fixed and our results could be used to determine if it is suitably small).
Suppose that we want to design a control law for the plant (31) using Method 2. The controller will be implemented digitally using a sampler and zero order hold element. As a first step in this direction we need to specify a discrete-time model of the plant (31), which describes the behavior of the system at sampling instants. We consider the difference equations corresponding to the exact plant model and its approximation respectively:

x(k + 1) = F

e
T
| (x(k), u(k)) | (32)
x(k + 1) = F

a
T
| (x(k), u(k)) | (33)

which are parameterized with the sampling period T. We emphasize that F

e
T

is not known in most cases. We will think of F

e
T

and F

a
T

as being defined
globally for all small T even though the initial value problem (31) may exhibit finite escape times. We do this by defining F

e
T

arbitrarily for pairs (x(k), u(k)) corresponding to finite escapes and noting that such points correspond only to points of arbitrarily large norm as T → 0, at least when f is locally bounded. So, the behavior of F

e
T will reflect the behavior of (31) as long as (x(k), uT (x(k))) remains bounded with a bound that is allowed to grow as T → 0. This is consistent with our main results that guarantee practical

Sampled-data control of nonlinear systems 13

asymptotic stability that is semiglobal in the sampling period, i.e., as T → 0 the set of points from which convergence to an arbitrarily small ball is guaranteed to contain an arbitrarily large neighborhood of the origin.
In general, one needs to use small sampling periods T since the approximate plant model is a good approximation of the exact model typically only for small T. It is clear then that we need to be able to obtain a controller uT (x) which is, in general, parameterized by T and which is defined for all small T. For simplicity, we consider only static state feedback controllers. For a fixed T > 0, consider systems (32), (33) with a given controller u(k) = uT (x(k)). We denote the state of the closed-loop system (32) (respectively (33)) with the given controller at time step k that starts from x(0) as x

e
(k, x(0)) or x

e
k

(respectively x

a
(k, x(0)) or x

a
k

). We introduce the error:

εk(ξ, z) := x

e
(k, ξ) − x

a
(k, z), | (34)

and also use the notation εk(ξ) := εk(ξ, ξ) = x

e
(k, ξ) − x

a
(k, ξ). In our
results (see Theorems 3 and 4), we will make a stability assumption on the family of closed-loop approximate plant models and will draw a conclusion about stability of the family of closed-loop exact plant models by invoking assumptions about the closeness of solutions between the two families.

One-step consistency The first type of closeness we will use is characterized in the following definition. It guarantees that the error between solutions starting from the same initial condition is small, over one step, relative to the size of the step. The terminology we use is based on that used in the numerical analysis literature (see [39]).

Definition 3. The family (uT , Fa
T

) is said to be one-step consistent with (uT , Fe
T

) if, for each compact set X ⊂ R

n, there exist a function ρ ∈ K∞ and T

∗ > 0 such that, for all x ∈ X and T ∈]0, T ∗ [, we have

|F

e
T

(x, uT (x)) − F

a
T
(x, uT (x))| ≤ T ρ(T) . | (35)

A sufficient condition for one-step consistency is the following:

Lemma 2. If

1. (uT , Fa
T

) is one-step consistent with (uT , F Euler
T

) where F

Euler
T

(x, u) :=
x + T f(x, u),
2. for each compact set X ⊂ R n there exist ρ ∈ K∞, M > 0, T

∗ > 0 such
that, for all T ∈]0, T ∗
[ and all x, y ∈ X ,
(a) |f(y, uT (x))| ≤ M,
(b) |f(y, uT (x)) − f(x, uT (x))| ≤ ρ(|y − x|),

then (uT , Fa
T

) is one-step consistent with (uT , Fe
T

).

14 D. Nešić and A.R. Teel

Multi-step consistency The second type of closeness we will use is characterized in terms of the functions F

e
T

, F

a
T

and uT (x) in the next definition. It will guarantee (see Lemma 3) that the error between solutions starting from the same initial condition is small over multiple steps corresponding “continuous-time” intervals with length of order one.
Definition 4. The family (uT , Fa
T

) is said to be multi-step consistent with (uT , Fe
T

) if, for each L > 0, η > 0 and each compact set X ⊂ R

n, there exist a
function α : R≥0×R≥0 → R≥0∪ {∞} and T

∗ > 0 such that, for all T ∈]0, T ∗ [
we have that {x, z ∈ X , |x − z| ≤ δ} implies

|F

e
T

(x, uT (x)) − F

a
T
(z, uT (z))| ≤ α(δ, T) | (36)

and

k ≤ L/T | =⇒ | α

k
(0, T) :=

k
z | }| | {
α (· · · α (α (0, T), T)· · · , T) ≤ η . (37)

In terms of trajectory error over “continuous-time” intervals with length of order one, multi-step consistency gives the following:
Lemma 3. If (uT , Fa
T

) is multi-step consistent with (uT , Fe
T

) then for each
compact set X ⊂ R

n, L > 0 and η > 0 there exists T >ˆ 0 such that, if T and ξ satisfy

T ∈]0, Tˆ[ , xa
k
(ξ) ∈ X ∀k : kT ∈ [0, L], | (38)

then

|εk(ξ)| ≤ η | ∀k : kT ∈ [0, L] . | (39)

An interesting sufficient condition for multi-step consistency is given in the following:
Lemma 4. If, for each compact set X ⊂ R

n, there exist K > 0, ρ ∈ K∞ and T

∗ > 0 such that for all T ∈]0, T ∗
[ and all x, z ∈ X we have

|F

e
T

(x, uT (x)) − F

a
T
(z, uT (z))| ≤ (1 + KT)|x − z| + T ρ(T) | (40)

then (uT , Fa
T

) is multi-step consistent with (uT , Fe
T

).
Relative to the one-step consistency condition, the condition of Lemma 4 is guaranteed by one-step consistency plus the following type of Lipschitz condition on either the family (uT , Fe
T

) or the family (uT , Fa
T

):
for each compact set X ⊂ R

n there exist K > 0 and T

∗ > 0 such that for all
x, z ∈ X and all T ∈]0, T ∗
[,
|FT (x, uT (x)) − FT (z, uT (z))| ≤ (1 + KT)|x − z| . | (41)

Sampled-data control of nonlinear systems 15

This condition is guaranteed for F

e
T when f(x, u) and uT (x) are locally Lipschitz (uniformly in small T). Note that no continuity assumptions on uT (x) were made in Lemma 2 to guarantee one-step consistency. The condition given in Lemma 4 for multi-step consistency is similar to conditions used in the numerical analysis literature (e.g., see conditions (i) and (iii) of Assumption 6.1.2 in [39, pg.429]).
One-step and multi-step consistency do not imply each other and this is one motivation for developing different stability theorems that rely on one of these properties. Example 4 in Section 3.3 shows that multi-step consistency may not hold when one-step consistency does hold. That one-step consistency may not hold when multi-step consistency does hold can be seen from the plant ẋ = x+u with Euler approximation x(k+ 1) = x(k)+T(x(k)+u(k)) = F

a
T

(x(k), u(k)) and controller uT (x) = −(

1
T + 1)x. The exact discrete-time model is x(k + 1) = e

T x(k) + (e

T −1)u(k) and we have F

a
T

(x, uT (x)) ≡ 0 and
F

e
T

(x, uT (x)) = ³
1 −

e

T −1
T

´
x. Since, for x in a compact set, F

e
T

(x, uT (x)) is
of order T we do not have one-step consistency. On the other hand, it follows from F

a
T

(x, uT (x)) ≡ 0 and the fact that F

e
T

(x, uT (x)) is of order T that we do have multi-step consistency. Indeed, for each compact set X ⊂ R and each η > 0 there exist strictly positive numbers K, T ∗
such that, for all x, z ∈ X , T ∈]0, T ∗
[, k ≥ 0,

|F

e
T

(x, uT (x)) − F

a
T

(z, uT (z))| = |F

e
T

(x, uT (x))| ≤ KT
:= α(δ, T) = α

k
(0, T) ≤ η .

### 3.2 Stability properties

We now give conditions on the family (uT , Fa
T

) that guarantee asymptotic stability for the family (uT , Fe
T

). As we have already seen in Example 3, it is not enough to assume simply that each member of the family (uT , Fa
| T ) is
asymptotically stable (at least for small T). Instead, we will impose partial uniformity of the stability property over all small T. For that, we make the following definitions:

Definition 5. Let β ∈ KL and let N ⊂ R

n be an open (not necessarily bounded) set containing the origin.

1. The family (uT , FT ) is said to be (β, N)-stable if there exists T

∗ > 0 such
that for each T ∈]0, T ∗
[, the solutions of the system
x(k + 1) = FT (x(k), uT (x(k))) | (42)

satisfy

|x(k, x(0))| ≤ β(|x(0)| , kT), ∀x(0) ∈ N, k ≥ 0. | (43)

16 D. Nešić and A.R. Teel

2. The family (uT , FT ) is said to be (β, N)-practically stable if for each R > 0 there exists T

∗ > 0 such that for each T ∈]0, T ∗ [ the solutions of
(42) satisfy:
|x(k, x(0))| ≤ β(|x(0)| , kT) + R, ∀x(0) ∈ N, k ≥ 0. | (44)

An equivalent Lyapunov formulation of (β, R

n)-stability is the following (local versions can also be formulated but are more tedious to state because of the need to keep track of basins of attraction):
Lemma 5. The following statements are equivalent:
1. There exists β ∈ KL such that the family (uT , FT ) is (β, R

n)-stable.
2. There exist T

∗ > 0, α1, α2 ∈ K∞, α3 ∈ K and for each T ∈]0, T ∗ [, VT :
R

n → R≥0 such that ∀x ∈ R

n, ∀T ∈]0, T ∗
[ we have:
α1(|x|) ≤ VT (x) ≤ α2(|x|), | (45)
VT (FT (x, uT (x))) − VT (x) ≤ −T α3(|x|), . | (46)
In our first main result (Theorem 3) we will show that if the family (uT , Fa
T

) is (β, N)-stable and multi-step consistent with (uT , Fe
T

) then the
family (uT , Fe
T

) is (β, N)-practically stable. We will also show (in Theorem 4) that the multi-step consistency assumption can be changed to a one-step consistency assumption when (β, N)-stability is formulated in terms of a family of Lyapunov functions satisfying (45),(46) and with an extra local Lipschitz condition that is uniform in small T.
Definition 6. The family (uT , FT ) is said to be equi-globally asymptotically stable (EGAS) by equi-Lipschitz Lyapunov functions if the second statement of Lemma 5 holds and, moreover, for each compact set X ⊂ R

n\ {0} there
exist M > 0 and T

∗ > 0 such that, for all x, z ∈ X and all T ∈]0, T ∗ [,

|VT (x) − VT (z)| ≤ M|x − z| . | (47)

Our first result is expressed in terms of trajectory bounds for (uT , Fa
T

)
and multi-step consistency:
Theorem 3. Let β ∈ KL and let N be a bounded neighborhood of the origin. If the family (uT , Fa
T

) is:
A: multi-step consistent with (uT , Fe
T

), and
B: (β, N)-stable,
then
C: the family (uT , Fe
T

) is (β, N)-practically stable. Our second result is expressed in terms of a family of Lyapunov functions for (uT , Fa
T

) and one-step consistency. It has some relations to the proof technique used to establish the main result of [7]. For simplicity we will only formulate the global result. Nonglobal results and results for stability of sets other than the origin can also be established with the same proof technique.

Sampled-data control of nonlinear systems 17

Theorem 4. If

A1: (uT , Fa
T

) is one-step consistent with (uT , Fe
T

), and
B1: (uT , Fa
T

) is EGAS by equi-Lipschitz Lyapunov functions

then

C1: there exists β ∈ KL such that, for each bounded neighborhood N of the origin, the family (uT , Fe
T

) is (β, N)-practically stable.

### 3.3 Examples

Example 4 illustrates Theorem 4 by giving an example where multi-step consistency does not hold but one-step consistency does hold and there is a suitable family of Lyapunov functions. Example 5 shows situation where each element of the family (uT , Fa
T

) is globally exponentially stable with overshoots uniform in T but where the family (uT , Fe
T

) fails to be (β, N)-
practically stable for any pair (β, N). In reference to Theorem 3, we use the notation C for this situation.

Example 4. Consider the two-input linear system

x˙ 1 = x1 + u1
x˙ 2 = u2

(48)

which has exact discretization

x1(k + 1) = e

T x1(k) + [e

T − 1]u1(k)
x2(k + 1) = x2(k) + T u2(k)

(49)

and Euler approximate discretization

x1(k + 1) = [1 + T]x1(k) + T u1(k) x2(k + 1) = x2(k) + T u2(k) .

(50)

Consider the controller

u(x) =

−2x1

0

- if 0 < 0.1x1 < x2 < 10x1

−2x1

−x2

- otherwise.

(51)

A1,A: It follows from Lemma 2 that (uT , Fa
T

) is one-step consistent
with (uT , Fe
T

). However, (uT , Fa
T

) is not multi-step consistent with (uT , Fe
T

).
Indeed, consider the initial condition (ξ1, ξ2) = (1, 0.1). It is easy to see that, in this case, (x

a
1

(k, ξ), xa
2

(k, ξ)) = (1 − T)

k
(1, 0.1), i.e., the positive

18 D. Nešić and A.R. Teel

ray x2 = 0.1x1 > 0 is forward invariant for all T ∈ (0, 1). On the other hand, (x

e
1

(1, ξ), xe
2

(1, ξ)) = ((2 − e

T
)1,(1 − T)0.1), i.e., for all small T > 0, x

e
2

(1, ξ) < 10x

e
1

(1, ξ) and x

e
2

(1, ξ) > 0.1x

e
1

(1, ξ) since e

T > 1 + T. It follows that, for k ≥ 1, x(k, ξ) will take values on the horizontal line given by x2 = (1 − T)0.1 moving in the direction of decreasing x1 until it crosses the positive ray x2 = 10x1. Let ¯k denote the number of steps required to cross the positive ray x2 = 10x1. It is easy to put an upper and lower bound on ¯kT that is independent of T. Then since, for all k ≤ ¯k, we have x
e
2

(k, ξ) = (1 − T)0.1
while x

a
2

(k, ξ) = (1 − T)

k0.1 ≤ e

−kT 0.1, it is clear that the conclusion of Lemma 3 is not satisfied. Hence (uT , Fa
T

) cannot be multi-step consistent with (uT , Fe
T

).
B1: We take VT (x) = |x1| + |x2|. We get, for T ∈ (0, 1) and 0 < 0.1x1 < x2 < 10x1:

VT (F

a
T

(x, uT (x))) − V (x) = −T|x1| ≤ − T 20

[|x1| + |x2|] | (52)

and, otherwise,

VT (F

a
T
(x, uT (x))) − V (x) = −T[|x1| + |x2|] . | (53)

It follows that the family (uT , Fa
T

) is EGAS by equi-Lipschitz Lyapunov functions.
C1: We conclude from Theorem 4 (and also using the homogeneity of VT (x) and F

e
T

(x, uT (x)) to pass from a semiglobal practical result to a global result and following the steps of the proof of Theorem 4 to get an exponential result) that the family (uT , Fe
T

) is (β, R

2
)-stable with β(s, t) of the form ks exp(−λt) with k > 0 and λ > 0.

Example 5. (A, B, C) Consider the double integrator, its Euler approximation and its exact discrete-time model:

double integrator: | ẋ1 = x2
x˙ 2 = u | (54)
approximate: x1(k + 1) = x1(k) + T x2(k)
x2(k + 1) = x2(k) + T u(k) | (55)
exact: x1(k + 1) = x1(k) + T x2(k) + 0.5T

2u(k)
x2(k + 1) = x2(k) + T u(k). | (56)
The following controller is designed for the Euler model:

u(x) = −

x1
T

−

2x2
T
. | (57)

C : The eigenvalues of the exact closed-loop are λ1 = 1−

T
2

, λ2 = −1, ∀T >
0 and thus the exact closed-loop model is not (β, N)-practically stable for any pair (β, N).

Sampled-data control of nonlinear systems 19
A : The eigenvalues of the Euler closed-loop system are λ1 = +√ 1 − T, λ2 =
−

√
1 − T. In a similar way as in the previous example we can show that there exists b > 0 such that for all T ∈]0, 0.5[ we have:

|x(k)| ≤ b exp(−0.5kT)|x(0)| , ∀x(0) ∈ R

2

Hence, the approximate closed-loop system is (β, R

2
)-stable with β(s, t) :=
b exp(−0.5t).
B : It now follows from Theorem 3 that (uT , Fa
T

) is not multi-step consistent with (uT , Fe
T

). In fact, (uT , Fa
T

) is not one-step consistent with (uT , Fe
| T

)
since

|²1(x)| =

¯
¯T
2
/2(−x1/T − 2x2/T)

¯
¯ = 2T |x1 + x2| , ∀x ∈ R
2
, ∀T.

### 4 Conclusion

Several recent results on design of sampled-data controllers that appeared in [21,27–31] were overviewed. These results are geared toward providing a unified framework for the digital controller design based either on the continuous-time plant model (Method 1) or on an approximate discrete-time plant model (Method 2). The conditions we presented are easily checkable and the results are applicable to a wide range of plants, controllers and system theoretic properties. Further research is needed to provide control design algorithms based on approximate discrete-time models. Our results on Method 2 provide a unified framework for doing so.

References

1. J. P. Barbot, S. Monaco, D. Normand-Cyrot and N. Pantalos, Discretization schemes for nonlinear singularly perturbed systems, Proc. CDC’91, pp. 443-448.
2. C. I. Byrnes and W. Lin, “Losslessness, feedback equivalence and the global stabilization of discrete-time systems”, IEEE Trans. Automat. Contr., 39 (1994), pp. 83-97.
3. B. Castillo, S. Di Gennaro, S. Monaco and D. Normand-Cyrot, On regulation under sampling, IEEE Trans. Automat. Contr., 42 (1997), pp. 864-868.
4. P. D. Christofides and A. R. Teel, Singular perturbations and input-to-state stability, IEEE Trans. Automat. Contr., 41 (1996), pp. 1645-1650.
5. T. Chen and B. A. Francis, Input-output stability of sampled-data systems, IEEE Trans. Automat. Contr., 36 (1991), pp. 50-58.
6. T. Chen and B. A. Francis, Optimal sampled-data control systems. Springer-Verlag: London, 1995.
7. F. H. Clarke, Y. S. Ledyaev, E. D. Sontag and A. I. Subbotin, Asymptotic controllability implies feedback stabilization, IEEE Trans. Automat. Contr., 42 (1997), pp. 1394-1407.
8. D. Dochain and G. Bastin, Adaptive identification and control algorithms for nonlinear bacterial growth systems, Automatica, 20 (1984), pp. 621-634.

20 D. Nešić and A.R. Teel

9. G. F. Franklin, J. D. Powell and M. L. Workman, Digital control of dynamic
| systems. Addison-Wesley Pub. Co. Inc.: Reading, 1990.
10. B. A. Francis and T. T. Georgiou, Stability theory for linear time-invariant
| plants with periodic digital controllers, IEEE Trans. Automat. Contr., vol. 33 (1988), pp. 820-832.
11. S. T. Glad, Output dead-beat control for nonlinear systems with one zero at
| infinity, Systems and Control Letters, 9 (1987), pp. 249-255.
12. G. C. Goodwin, B. McInnis and R. S. Long, Adaptive control algorithm for
| waste water treatment ad pH neutralization, Optimal Contr. Applic. Meth., 3 (1982), pp. 443-459.
13. L. Grüne, Input-to-state stability of exponentially stabilized semi-linear control
| systems with inhomogeneous perturbations, preprint (1998).
14. L. Hou, A. N. Michel and H. Ye, Some qualitative properties of sampled-data
| control systems, IEEE Trans. Automat. Contr., 42 (1997), pp. 1721-1725.
15. P. Iglesias, Input-output stability of sampled-data linear time-varying systems,
| IEEE Trans. Automat. Contr., 40 (1995), pp. 1646-1650.
16. A. Iserles and G. Söderlind, Global bounds on numerical error for ordinary
| differential equations, J. Complexity, 9 (1993), pp. 97-112.
17. N. Kazatzis and C. Kravaris, System-theoretic properties of sampled-data rep-
| resentations of nonlinear systems obtained via Taylor-Lie series, Int. J. Control, 67 (1997), pp. 997-1020.
18. H. K. Khalil, Nonlinear systems. Prentice-Hall: New Jersey, 1996.
19. P.E. Kloeden and J. Lorenz. Stable attracting sets in dynamical systems and
| their one-step discretizations, SIAM J. Num. Anal., 23 (1986), pp. 986-995.
20. B. C. Kuo, Digital control systems. Saunders College Publishing: Ft. Worth,
| 1992.
21. D. S. Laila and D. Nešić, A note on preservation of dissipation inequalities
| under sampling: the dynamic feedback case, submitted to Amer. Contr. Conf.,
| 2001.
22. V. Lakshmikantham and S. Leela, Differential and integral inequalities, vol. 1.
| Academic Press: New York, 1969.
23. I. M. Y. Mareels, H. B. Penfold and R. J. Evans, Controlling nonlinear time-
| varying systems via Euler approximations, Automatica, 28 (1992), pp. 681-696.
24. S. Monaco and D. Normand-Cyrot, Zero dynamics of sampled nonlinear sys-
| tems, Syst. Contr. Lett., 11 (1988), pp. 229-234.
25. S. Monaco and D. Normand-Cyrot, Sampling of a linear analytic control system,
| Proc. CDC’85, pp. 1457-1462.
26. M. S. Mousa, R. K. Miller and A. N. Michel, Stability analysis of hybrid compos-
| ite dynamical systems: descriptions involving operators and difference equations, IEEE Trans. Automat. Contr., 31 (1986), pp. 603-615.
27. D. Nešić, A. R. Teel and E.D.Sontag, Formulas relating KL stability estimates of
| discrete-time and sampled-data nonlinear systems, Sys. Contr. Lett., 38 (1999), pp. 49-60.
28. D. Nešić, A. R. Teel and P. V Kokotović, Sufficient conditions for stabilization
| of sampled-data nonlinear systems via discrete-time approximations, Syst. Contr. Lett., 38 (1999), pp. 259-270.
29. D. Nešić and A. R. Teel, Set stabilization of sampled-data differential inclusions
| via their approximate discrete-time models, to appear in Conf. Decis. Contr., Sydney, 2000.

Sampled-data control of nonlinear systems 21

30. D. Nešić, D. S. Laila and A. R. Teel, On preservation of dissipation inequalities under sampling, to appear in Conf. Decis. Contr., Sydney, 2000.
31. D. Nešić and P. Dower, Further results on preservation of input-to-state stability under sampling, to appear in ICARV, Singapore, 2000.
32. R. Ortega and D. Taoutaou, A globally stable discrete-time controller for current-fed induction motors, Systems and Control Letters, 28 (1996), pp. 123-128.
33. D. H. Owens, Y. Zheng and S. A. Billings, Fast sampling and stability of nonlinear sampled-data systems: Part 1. Existence theorems, IMA J. Math. Contr. Informat., 7 (1990), pp. 1-11.
34. Z. Qu, Robust control of nonlinear uncertain systems. John Wiley & Sons: New York, 1998.
35. E. D. Sontag, Smooth stabilization implies coprime factorization, IEEE Trans. Automat. Contr., 34 (1989), 435-443.
36. E. D. Sontag, Remarks on stabilization and input-to-state stability, in Proc. CDC, Tampa, USA, 1989.
37. S. A. Svoronos, D. Papageorgiou and C. Tsiligiannis, Discretization of nonlinear control systems via the Carleman linearization, Chemical Eng. Science, 49 (1994), pp. 3263-3267.
38. H. J. Stetter, Analysis of discretization methods for ordinary differential equations. Springer-Verlag: New York, 1973.
39. A. M. Stuart and A. R. Humphries, Dynamical systems and numerical analysis. Cambridge University Press: New York, 1996.
40. A. R. Teel, Connection between Razumikhin-type theorems and the ISS nonlinear small gain theorem, IEEE Trans. Automat. Contr., to appear, 1998.
41. A. R. Teel, D. Nešić and P. V. Kokotović, A note on input-to-state stability of sampled-data nonlinear systems, In Proceedings of the 37th IEEE Conference on Decision and Control, Tampa, Florida, 1998.
42. Y. Zheng, D. H. Owens and S. A. Billings, Fast sampling and stability of nonlinear sampled-data systems: Part 2: Sampling rate estimation, IMA J. Math. Contr. Informat., 7 (1990), pp. 13-33.

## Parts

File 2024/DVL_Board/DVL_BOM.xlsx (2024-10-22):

Part name | part number/model | unit price | quantity | link | project | has been bought | Needed by
Ethernet Female | ARJM11D7-009-NN-EW2 | 3.95 | 3? | https://www.digikey.com/en/products/detail/abracon-llc/ARJM11D7-009-NN-EW2/7675212 | DVL board | no |  | DVL cost per board
UART to USB chip | FT230XS-R | 2.26 | 3? | https://www.digikey.com/en/products/detail/ftdi-future-technology-devices-international-ltd/FT230XS-R/3029141 | DVL board | no |  | 9.916
micro USB type B female | any | 0.56 | 3 | https://www.digikey.com/en/products/detail/amphenol-cs-fci/10118194-0001LF/2785389 | DVL board | no
50 ohm 1206 resistor |  | 0.10 | 4 x 3 | https://www.digikey.com/en/products/detail/yageo/RC1206JR-0747RL/2827653 | DVL board
27 Ohm 1206 resistor |  | 0.10 | 4 x 3 | https://www.digikey.com/en/products/detail/yageo/RC1206JR-0727RL/729261 | DVL board |  |  | full digikey cart link:
4.7 uF 1206 |  | 0.22 | 1 x 3 | https://www.digikey.com/en/products/detail/tdk-corporation/C3216X7R1E475K160AC/634397 | DVL board |  |  | https://www.digikey.com/short/nhn4zdmz
100 nF 1206 |  | 0.10 | 2 x 3 | https://www.digikey.com/en/products/detail/walsin-technology-corporation/1206B104K500CT/9355102 | DVL board
47 pF 1206 |  | 0.11 | 2 x 3 | https://www.digikey.com/en/products/detail/w%C3%BCrth-elektronik/885012008041/5453740 | DVL board
10 nF 1206 |  | 0.21 | 1 x 3 | https://www.digikey.com/en/products/detail/yageo/CC1206KRX7R9BB103/302908 | DVL board

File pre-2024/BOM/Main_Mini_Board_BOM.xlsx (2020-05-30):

Comment | Supplier Link | Description | DesignatorB1 | DesignatorB2 | Footprint | Quantity B1 | Quantity B2 | Quantity Req | Requested Quantity | Price at req quant | Total Price
Push Button | https://www.digikey.com/product-detail/en/te-connectivity-alcoswitch-switches/FSM101/450-1157-ND/701084 | Tactile Switch SPST-NO Top Actuated Through Hole | B1 | B1 | PUSH BUTTON | 1 | 1 | 3 | 3 | 0.37 | 1.11
Cap 22uF | https://www.digikey.com/product-detail/en/samsung-electro-mechanics/CL31X226KAHN3NE/1276-3299-1-ND/3891385 | Ceramic Capacitor | C1, C2, C3, C13, C15, C25 | C13, C23 | C1206 | 6 | 2 | 12 | 12 | 0.729 | 8.75
Cap 3.3uF | https://www.digikey.com/product-detail/en/tdk-corporation/CGA5L1X8L1H335K160AC/445-175271-1-ND/7930966 | Ceramic Capacitor | C4, C16 | C1, C14 | C1206 | 2 | 2 | 6 | 6 | 0.85 | 5.1
Cap 10nF | https://www.digikey.com/product-detail/en/w-rth-elektronik/885012208112/732-12140-1-ND/9346160 | Ceramic Capacitor | C5, C17, C43, C44, C47, C50 | C4, C5, C8, C11, C15 | C1206 | 6 | 5 | 16.5 | 17 | 0.096 | 1.63
Cap 100pF | https://www.digikey.com/product-detail/en/samsung-electro-mechanics/CL31C101KBCNNNC/1276-2802-1-ND/3890888 | Ceramic Capacitor | C6, C11, C18,C23, C32 | C16, C21 | C1206 | 5 | 2 | 10.5 | 11 | 0.107 | 1.18
Cap 4.7uF | https://www.digikey.com/product-detail/en/taiyo-yuden/UMK316AB7475KL-T/587-2994-1-ND/2714187 | Ceramic Capacitor | C7, C19, C31 | C17 | C1206 | 3 | 1 | 6 | 6 | 0.38 | 2.28
HMK325C7475KN-TE | https://www.digikey.com/product-detail/en/taiyo-yuden/HMK325C7475KN-TE/587-5038-1-ND/6563881 | Capacitor (Semiconductor SIM Model) 4.7uF | C27, C28, C30, C35, C36, C38, C40, C41, C55, C56 | C29 | C1210 | 10 | 1 | 16.5 | 16 | 0.992 | 15.87
Cap 1nF | https://www.digikey.com/product-detail/en/würth-elektronik/885012208075/732-8115-1-ND/5454742 | Ceramic Capacitor | C8, C9, C20, C21, C54 | C10, C18, C19 | C1206 | 5 | 3 | 12 | 12 | 0.086 | 1.03
Cap 220nF | https://www.digikey.com/product-detail/en/samsung-electro-mechanics/CL31B224KBFNNNE/1276-1106-1-ND/3889192 | Ceramic Capacitor | C10, C12, C22, C24 | C20, C22 | C1206 | 4 | 2 | 9 | 10 | 0.089 | 0.89
Cap 47nF | https://www.digikey.com/product-detail/en/würth-elektronik/885012208116/732-12230-1-ND/9346250 | Ceramic Capacitor | C29 |  | C1206 | 1 |  | 1.5 | 2 | 0.13 | 0.26
Cap 100nF | https://www.digikey.com/product-detail/en/kemet/C1206C104K5RAC7800/399-C1206C104K5RAC7800CT-ND/411524 | Ceramic Capacitor | C33, C45, C46, C53 | C6, C7, C26 | C1206 | 4 | 3 | 10.5 | 11 | 0.088 | 0.97
Cap 15nF | https://www.digikey.com/product-detail/en/würth-elektronik/885012208082/732-8122-1-ND/5454749 | Ceramic Capacitor | C34 |  | C1206 | 1 |  | 1.5 | 2 | 0.12 | 0.24
Cap 1uF | https://www.digikey.com/product-detail/en/w-rth-elektronik/885012208036/732-7692-1-ND/5454319 | Ceramic Capacitor | C42 | C2, C9 | C1206 | 1 | 2 | 4.5 | 5 | 0.15 | 0.75
Cap 47pF | https://www.digikey.com/product-detail/en/würth-elektronik/885012008041/732-7885-1-ND/5454512 | Ceramic Capacitor | C51, C52 | C12, C25 | C1206 | 2 | 2 | 6 | 6 | 0.11 | 0.66
Cap 10uF | https://www.digikey.com/product-detail/en/tdk-corporation/C3216X7R1H106K160AC/445-181601-1-ND/9991479 | Ceramic Capacitor | C48, C49 | C27, C28 | C1206 | 2 | 2 | 6 | 6 | 0.93 | 5.58
Cap 33uF | https://www.digikey.com/product-detail/en/nichicon/UUX1J330MNL6GS/493-9972-1-ND/3974043 | CAP ALUM 33UF 20% 63V SMD | C37, C39 |  | UUX1J330MNL6GS | 2 |  | 3 | 3 | 0.48 | 1.44
Cap 390uF | https://www.digikey.com/product-detail/en/nichicon/PCV1E391MCL2GS/493-4544-1-ND/2786841 | CAP ALUM POLY 390UF 20% 25V SMD | C14, C26 | C24, C3(spect for 330uF) | PCVXXXXXMCLXGS | 2 | 2 | 6 | 6 | 4.17 | 25.02
MMSZ5230B | https://www.digikey.com/product-detail/en/micro-commercial-co/MMSZ5230B-TP/MMSZ5230B-TPMSCT-ND/4885342 | Zener Voltage Regulator, 500 mW, 2-Pin SOD-123, Pb-Free, Tape and Reel | D4, D9 | D8 | ONSC-SOD-123-2-425-04_V | 2 | 1 | 4.5 | 5 | 0.2 | 1
MBRS340 | https://www.digikey.com/product-detail/en/vishay-semiconductor-diodes-division/VS-MBRS340-M3-9AT/112-VS-MBRS340-M3-9ATCT-ND/10718847 | Schottky Rectifier | D5, D6, D10, D11 | D9, D10 | MBRS340 | 4 | 2 | 9 | 10 | 0.347 | 3.47
SCHOTTKY | https://www.digikey.com/product-detail/en/infineon-technologies/BAS170WE6327HTSA1/BAS170WE6327HTSA1CT-ND/3819495 | DIODE SCHOTTKY 70V 70MA SOD323-2 | D12 |  | BAS170W | 1 |  | 1.5 | 2 | 0.48 | 0.96
RGB LED Strip | https://www.digikey.com/product-detail/en/american-bright-optoelectronics-corporation/AB-FA01206-19700-XA2/2007-AB-FA01206-19700-XA2CT-ND/10270640 | LED RGB Strip - Bare Nonaddressable | D13 | D1 | HEADER 1X4 | 1 | 1 | 3 | 3 | 1.43 | 4.29
1N58xx | https://www.digikey.com/product-detail/en/comchip-technology/SS24-HF/641-SS24-HFCT-ND/10443817 | 1A Schottky Barrier Rectifier Diode | D2, D3, D7, D8, D14, D15, D16 | D2, D3, D4, D6, D7 | 1N58XX | 7 | 5 | 18 | 18 | 0.242 | 4.36
Molex 43045-0402 | https://www.digikey.com/products/en?keywords=Molex 43045-0402 | Micro-Fit 3.0 Right Angle Header, 3.00mm Pitch, Dual Row, 4 Circuits, with Snap-in Plastic Peg PCB Lock, Gold, Glow Wire Capable, Black | J1, J2, J3, J5, J6, J7, J8 | J1, J2, J3 | MOLEX43045-0402 | 7 | 3 | 15 | 0 | 2.03 | 0 | Hav some in inventory
Molex0470533000 | https://www.digikey.com/product-detail/en/molex/0470533000/WM9797-ND/3262217 | GPU Connector | J4 |  | HEADER 1X4 12V | 1 |  | 1.5 | 2 | 0.46 | 0.92
Molex0470541000 | https://www.digikey.com/products/en/connectors-interconnects/rectangular-connectors-housings/319?k=470541000 | GPU Connector |  |  |  | 1 |  | 1.5 | 2 | 0.1 | 0.2
Molex0008500114 | https://www.digikey.com/product-detail/en/molex/0008500114/WM1114-ND/26475 | GPU Connector |  |  |  | 4 |  | 6 | 10 | 0.163 | 1.63
IHLP-6767DZ-11 | https://www.digikey.com/product-detail/en/vishay-dale/IHLP6767GZER150M11/541-1287-1-ND/2139413 | 15µH Shielded Molded Inductor 14A 14.4 mOhm Max Nonstandard | L1, L2 |  | IHLP-6767DZ-11 | 2 |  | 3 | 3 | 5.87 | 17.61
SRR1240-4R7M | https://www.digikey.com/product-detail/en/bourns-inc/SRR1240-4R7M/SRR1240-4R7MCT-ND/2127398 | FIXED IND 4.7UH 6A 18 MOHM SMD |  | L1 | SRR1240 |  | 1 | 1.5 | 2 | 1.25 | 2.5
PQ2617BHA-330K | https://www.digikey.com/product-detail/en/bourns-inc/PQ2617BHA-330K/PQ2617BHA-330K-ND/7695918 | 33µH Shielded Wirewound Inductor 28A 2.5mOhm Max Nonstandard | L3 |  | PQ2617BHA-330K | 1 |  | 1.5 | 2 | 4.65 | 9.3
Molex2002411114 | https://www.digikey.com/product-detail/en/2002411114/900-2002411114-ND/10709042?WT.z_cid=ref_neda_dkc_buynow | Board to board connection | P1 | P1 | Molex2002411114 | 1 | 1 | 3 | 3 | 1.87 | 5.61
Molex0768230343 | https://www.digikey.com/product-detail/en/molex/0768230343/900-0768230343CT-ND/11192252 | Board to board connection |  |  |  | 8 | 8 | 24 | 30 | 0.2424 | 7.27
Molex2004561214 | https://www.digikey.com/product-detail/en/2004561214/900-2004561214-ND/10709201?WT.z_cid=ref_neda_dkc_buynow | Board to board connection |  |  |  | 2 | 2 | 6 | 6 | 0.86 | 5.16
Header 8X3 | https://www.digikey.com/product-detail/en/samtec-inc/TMMH-108-01-T-T/SAM12190-ND/6692344 | Connector Header Through Hole 24 position 0.079" (2.00mm) | P4, P6 | P2, P4 | HEADER 8X3 | 2 | 2 | 6 | 6 | 1.58 | 9.48
Header 4 |  | Header, 4-Pin | P4, P6 | P2, P7 | HEADER 1X4 | 2 | 2 | 6 |  |  | 0
DF13-4P-1.25DSA | https://www.digikey.com/product-detail/en/DF13-4P-1.25DSA/H2193-ND/241767 | Header, 4-Pin | P5, P7 | P3, P5 | DF13-4P-1.25DSA | 2 | 2 | 6 | 6 | 0.43 | 2.58
FTSH-105-01-L-DV-K-TR | https://www.digikey.com/product-detail/en/samtec-inc/FTSH-105-01-L-DV-K-TR/SAM13165CT-ND/8827920 | CONN HEADER 10POS DUAL .05" SMD | P8 | P8 | FTSH-105-01-L-DV-K-TR | 1 | 1 | 3 | 3 | 3.6 | 10.8
Header 4 |  | Header, 4-Pin | P9 | P9 | HDR1X4 | 1 | 1 | 3 |  |  | 0
FDD9410-F085 | https://www.digikey.com/product-detail/en/on-semiconductor/FDD9410-F085/FDD9410-F085CT-ND/5140672 | N-Channel TrenchMOS Intermediate Level FET, 40 V, 50 A, 3-Pin SOT428, Tape and Reel | Q2, Q3, Q4, Q5, Q6, Q7, Q8, Q9 | Q5, Q6, Q7, Q8 | NXP-SOT428_M | 8 | 4 | 18 | 18 | 0.821 | 14.78
BSC028N06LS3 | https://www.digikey.com/product-detail/en/infineon-technologies/BSC028N06LS3GATMA1/BSC028N06LS3GATMA1CT-ND/2231029 | N-Channel MOSFET | Q10, Q11 |  | BSC028N06LS3 | 2 |  | 3 | 3 | 2.51 | 7.53
DMN1019USN | https://www.digikey.com/product-detail/en/diodes-incorporated/DMN1019USN-13/DMN1019USN-13DICT-ND/4898885 | 12V N-Channel Enhancement Mode MOSFET | Q12, Q13, Q14, Q15, Q16, Q17 | Q1, Q2, Q3, Q4, Q9, Q10 | SOT-23 | 6 | 6 | 18 | 18 | 0.347 | 6.25
Res 0 | https://www.digikey.com/product-detail/en/yageo/RC0603JR-070RL/311-0.0GRCT-ND/729622 | Jumper | R37 | R11 | R0603 | 1 | 1 | 3 | 0 |  | 0 | Ordered extras with merge board
Res 8.06k | https://www.digikey.com/product-detail/en/stackpole-electronics-inc/RMCF0603FT8K06/RMCF0603FT8K06CT-ND/2418150 | Resistor |  | R21 | R0603 |  | 1 | 1.5 | 10 | 0.016 | 0.16
Res 1k | https://www.digikey.com/product-detail/en/stackpole-electronics-inc/RMCF0603JT1K00/RMCF0603JT1K00CT-ND/1943173 | Resistor | R38, R40, R42 | R23, R25, R27 | R0603 | 3 | 3 | 9 | 10 | 0.014 | 0.14
Res 27 | https://www.digikey.com/product-detail/en/stackpole-electronics-inc/RMCF0603JT27R0/RMCF0603JT27R0CT-ND/2418191 | Resistor | R35, R36 | R19, R22 | R0603 | 2 | 2 | 6 | 10 | 0.014 | 0.14
Res 4.7k | https://www.digikey.com/product-detail/en/stackpole-electronics-inc/RMCF0603JT4K70/RMCF0603JT4K70CT-ND/1943184 | Resistor | R33, R34 | R6, R7 | R0603 | 2 | 2 | 6 | 10 | 0.014 | 0.14
Res 20 | https://www.digikey.com/product-detail/en/koa-speer-electronics-inc/RK73B1JTTD200J/2019-RK73B1JTTD200JCT-ND/9846827 | Resistor | R27, R28, R29, R30 | R2, R3, R4, R5 | R0603 | 4 | 4 | 12 | 12 | 0.014 | 0.17
Res 47k | https://www.digikey.com/product-detail/en/stackpole-electronics-inc/RMCF0603JT47K0/RMCF0603JT47K0CT-ND/1943199 | Resistor | R18 | R10 | R0603 | 1 | 1 | 3 | 10 | 0.014 | 0.14
Res 15k | https://www.digikey.com/product-detail/en/stackpole-electronics-inc/RMCF0603JG15K0/RMCF0603JG15K0CT-ND/4425129 | Resistor | R26 |  | R0603 | 1 |  | 1.5 | 10 | 0.014 | 0.14
Res 10k | https://www.digikey.com/product-detail/en/stackpole-electronics-inc/RMCF0603JT10K0/RMCF0603JT10K0CT-ND/1943191 | Resistor | R24, R31, R39, R41, R43 | R8, R24, R26, R28 | R0603 | 5 | 4 | 13.5 | 14 | 0.014 | 0.2
Res 390k | https://www.digikey.com/product-detail/en/koa-speer-electronics-inc/RK73B1JTTD394J/2019-RK73B1JTTD394JCT-ND/9846870 | Resistor | R23 |  | R0603 | 1 |  | 1.5 | 10 | 0.014 | 0.14
Res 30.1k | https://www.digikey.com/product-detail/en/stackpole-electronics-inc/RMCF0603FG30K1/RMCF0603FG30K1CT-ND/4425041 | Resistor | R22 |  | R0603 | 1 |  | 1.5 | 10 | 0.016 | 0.16
Res 2k | https://www.digikey.com/product-detail/en/stackpole-electronics-inc/RMCF0603FT113K/RMCF0603FT113KCT-ND/2417911 | Resistor | R20, R32 | R9 | R0603 | 2 | 1 | 4.5 | 10 | 0.014 | 0.14
Res 113k | https://www.digikey.com/product-detail/en/stackpole-electronics-inc/RMCF0603FT113K/RMCF0603FT113KCT-ND/2417911 | Resistor | R19 | R20 | R0603 | 1 | 1 | 3 | 10 | 0.016 | 0.16
Res 21k | https://www.digikey.com/product-detail/en/stackpole-electronics-inc/RMCF0603FT21K0/RMCF0603FT21K0CT-ND/2417985 | Resistor |  | R1 | R0603 |  | 1 | 1.5 | 10 | 0.016 | 0.16
Res 20k | https://www.digikey.com/product-detail/en/koa-speer-electronics-inc/RK73B1JTTD203J/2019-RK73B1JTTD203JCT-ND/9846782 | Resistor | R10 |  | R0603 | 1 |  | 1.5 | 10 | 0.014 | 0.14
Res 280k | https://www.digikey.com/product-detail/en/koa-speer-electronics-inc/RK73H1JTTD2803F/2019-RK73H1JTTD2803FCT-ND/9847056 | Resistor | R9 |  | R0603 | 1 |  | 1.5 | 10 | 0.022 | 0.22
Res 100 | https://www.digikey.com/product-detail/en/yageo/RC0603FR-07100RL/311-100HRCT-ND/729835 | Resistor | R5, R8, R14, R17 | R15, R18 | R0603 | 4 | 2 | 9 | 10 | 0.023 | 0.23
Res 51k | https://www.digikey.com/product-detail/en/stackpole-electronics-inc/RMCF0603JT51K0/RMCF0603JT51K0CT-ND/1943200 | Resistor | R3, R12 | R13 | R0603 | 2 | 1 | 4.5 | 10 | 0.014 | 0.14
Res 100k | https://www.digikey.com/product-detail/en/susumu/RR0816P-104-D/RR08P100KDCT-ND/432772 | Resistor | R2, R4, R11, R13, R25 | R12, R14 | R0603 | 5 | 2 | 10.5 | 10 | 0.093 | 0.93
Res 18m | https://www.digikey.com/product-detail/en/yageo/RL1206FR-070R018L/311-018LWCT-ND/3885377 | Resistor | R6, R7, R15, R16 | R16, R17 | R1206 | 4 | 2 | 9 | 10 | 0.378 | 3.78
Res 3m | https://www.digikey.com/product-detail/en/rohm-semiconductor/PMR50HZPJV3L0/RHM-003ATCT-ND/2094555 | Resistor | R21 |  | 12Z-2010 | 1 |  | 1.5 | 2 | 0.56 | 1.12
LTC3780EG#PBF | https://americas.rsdelivers.com/product/analog-devices/ltc3780egpbf/analog-devices-ltc3780egpbf-dc-dc-buck-controller/7869950 (https://www.digikey.com/products/en?keywords=LTC3780EG%23PBF) | Buck-boost Controller, Constant Frequency, Current Mode Control with Power Good Output, 24-pin SOP (G-24), -40 to 85 degC, Pb-Free | U1, U2 | U3 | LT-G-24_L | 2 | 1 | 4.5 | 5 | 10.85 | 54.25 | Out of stock in US
LTC3769 | https://www.digikey.com/product-detail/en/linear-technology-analog-devices/LTC3769EFE-PBF/LTC3769EFE-PBF-ND/4964736 | 48V Switching converter | U3 |  | LTC3769 | 1 |  | 1.5 | 2 | 7.19 | 14.38
EFM32PG12B500F1024IM48-C | https://www.digikey.com/product-detail/en/silicon-labs/EFM32PG12B500F1024IM48-C/336-5333-ND/8161157 | ARM® Cortex®-M4 Pearl Gecko Microcontroller IC 32-Bit 40MHz 1MB (1M x 8) FLASH 48-QFN (7x7) | U4 | U1 | QFN50P700X700X90-49N | 1 | 1 | 3 | 3 | 4.63 | 13.89
R-78E9.0-0.5 | https://www.digikey.com/product-detail/en/recom-power/R-78E9-0-0-5/945-2638-5-ND/6010095 | .5A DC/DC Voltage Converter | U8 |  |  | 1 |  | 1.5 | 2 | 2.89 | 5.78
R-78E3.3-1.0 | https://www.digikey.com/product-detail/en/recom-power/R-78E3-3-1-0/945-2409-5-ND/5327711 | 1A DC/DC Voltage Converter | U5 | U6 | R-78EXX-1.0 | 1 | 1 | 3 | 3 | 3.26 | 9.78
Micro USB | https://www.digikey.com/product-detail/en/molex-llc/1050170001/WM1399CT-ND/2350885 | USB - micro B USB 2.0 Receptacle Connector 5 Position Surface Mount, Right Angle | U6 | U5 | MICRO USB | 1 | 1 | 3 | 3 | 0.91 | 2.73
FT230x | https://www.digikey.com/product-detail/en/ftdi-future-technology-devices-international-ltd/FT230XS-R/768-1135-1-ND/3029155 | USB to Basic UART IC | U7 | U4 | FT230X | 1 | 1 | 3 | 3 | 2.04 | 6.12
PTN78020WAH | https://www.digikey.com/products/en?keywords=PTN78020WAH | 6A DC DC Converter |  | U2 | PTN78020WAH |  | 1 | 1.5 | 1 | 25.44 | 25.44
Cart link: | https://www.digikey.com/short/zjdq03 |  | Other links: | https://americas.rsdelivers.com/product/analog-devices/ltc3780egpbf/analog-devices-ltc3780egpbf-dc-dc-buck-controller/7869950 (https://www.digikey.com/products/en?keywords=LTC3780EG%23PBF) | Order Quantity: | 5 |  |  |  | Total: | 329.38 | Does not include shipping, tarrifs, or tax

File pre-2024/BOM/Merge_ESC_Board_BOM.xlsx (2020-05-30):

Comment | Digikey link | Other distributor link | Description | Designator | Footprint | LibRef | Quantity Per Board | x1.5 Required Quantity | Recomended Quantity | Total price
Cap 1u | https://www.digikey.com/product-detail/en/w-rth-elektronik/885012208036/732-7692-1-ND/5454319 |  | Capacitor (Semiconductor SIM Model) | C1, C2 | C1206 | Cap Semi | 2 | 6 | 6 | 0.9
Cap 10n | https://www.digikey.com/product-detail/en/w-rth-elektronik/885012208112/732-12140-1-ND/9346160 |  | Capacitor (Semiconductor SIM Model) | C3_ESC1, C3_ESC2, C3_ESC3, C3_ESC4, C3_ESC5, C3_ESC6, C3_ESC7, C3_ESC8, C4_ESC1, C4_ESC2, C4_ESC3, C4_ESC4, C4_ESC5, C4_ESC6, C4_ESC7, C4_ESC8, C5_ESC1, C5_ESC2, C5_ESC3, C5_ESC4, C5_ESC5, C5_ESC6, C5_ESC7, C5_ESC8 | C1206 | Cap Semi | 24 | 72 | 72 | 6.91
1N5819 | https://www.digikey.com/product-detail/en/comchip-technology/SS24-HF/641-SS24-HFCT-ND/10443817 |  | 1A Schottky Barrier Rectifier Diode | D1_ESC1, D1_ESC2, D1_ESC3, D1_ESC4, D1_ESC5, D1_ESC6, D1_ESC7, D1_ESC8 | 1N58xx | 1N58xx | 8 | 24 | 25 | 5.22
Jumper | https://www.digikey.com/product-detail/en/yageo/RC0603JR-070RL/311-0.0GRCT-ND/729622 |  | Resistor | J1_ESC1, J1_ESC2, J1_ESC3, J1_ESC4, J1_ESC5, J1_ESC6, J1_ESC7, J1_ESC8, J2_ESC1, J2_ESC2, J2_ESC3, J2_ESC4, J2_ESC5, J2_ESC6, J2_ESC7, J2_ESC8, J3_ESC1, J3_ESC2, J3_ESC3, J3_ESC4, J3_ESC5, J3_ESC6, J3_ESC7, J3_ESC8, J4_ESC1, J4_ESC2, J4_ESC3, J4_ESC4, J4_ESC5, J4_ESC6, J4_ESC7, J4_ESC8, J5_ESC1, J5_ESC2, J5_ESC3, J5_ESC4, J5_ESC5, J5_ESC6, J5_ESC7, J5_ESC8, J6_ESC1, J6_ESC2, J6_ESC3, J6_ESC4, J6_ESC5, J6_ESC6, J6_ESC7, J6_ESC8, J7_ESC1, J7_ESC2, J7_ESC3, J7_ESC4, J7_ESC5, J7_ESC6, J7_ESC7, J7_ESC8, J8_ESC1, J8_ESC2, J8_ESC3, J8_ESC4, J8_ESC5, J8_ESC6, J8_ESC7, J8_ESC8 | J1-0603 | Res3 | 24 | 72 | 100 | 0.77
Molex42820-4224 | Not stocked | https://www.mouser.com/ProductDetail/Molex/42820-4224?qs=c8NFF48pVsBxdq815tBX5w%3D%3D |  | P1, P2 | Molex42820-4224 | Molex42820-4224 | 2 | 6 | 6 | 49.92
Header 2 |  |  | Header, 2-Pin | P3 | HDR1X2 | Header 2 | 1 | 3
Molex2002411114 | https://www.digikey.com/product-detail/en/2002411114/900-2002411114-ND/10709042?WT.z_cid=ref_neda_dkc_buynow |  |  | P4 | MOLEX2002411114 | Molex2002411114 | 1 | 3 | 3 | 5.61
Header 4 |  |  | Header, 4-Pin | P5 | HDR1X4 | Header 4 | 1 | 3
Motor Connector | https://www.digikey.com/product-detail/en/molex/0768290102/WM16836-ND/7604320 |  |  | P6_ESC1, P6_ESC2, P6_ESC3, P6_ESC4, P6_ESC5, P6_ESC6, P6_ESC7, P6_ESC8 | 76829-0102 | Megafit Slim Vert 2 Peg | 8 | 24 | 24 | 19.97
IPT004N03L | Out of stock: https://www.digikey.com/product-detail/en/infineon-technologies/IPT004N03LATMA1/IPT004N03LATMA1CT-ND/4571877 | https://www.newark.com/infineon/ipt004n03latma1/mosfet-n-ch-30v-300a-pg-hsof-8/dp/97Y1840?CMP=AFC-OP | N-Channel OptiMOS(TM) Power-MOSFET, 30 V VDS, 300 A ID, -55 to 175 degC, PG-HSOF-8, Reel, Green | Q1, Q2 | INF-PG-HSOF-8-1_V | IPT004N03L | 2 | 6 | 6 | 33.36
CSD16570Q5B | https://www.digikey.com/product-detail/en/texas-instruments/CSD16570Q5B/296-47753-1-ND/8133102 |  | MOSFET N-CH 25V 100A 8VSON | Q3_ESC1, Q3_ESC2, Q3_ESC3, Q3_ESC4, Q3_ESC5, Q3_ESC6, Q3_ESC7, Q3_ESC8 | CSD16570Q5B | CSD16570Q5B | 8 | 24 | 25 | 46.16
Res 100 | https://www.digikey.com/product-detail/en/yageo/RC0603FR-07100RL/311-100HRCT-ND/729835 |  | Resistor | R1, R2 | J1-0603 | Res3 | 2 | 6 | 10 | 0.23
Res 100k | https://www.digikey.com/product-detail/en/koa-speer-electronics-inc/RK73B1JTTD104J/2019-RK73B1JTTD104JCT-ND/9846744 |  | Resistor | R3, R4 | J1-0603 | Res3 | 2 | 6 | 10 | 0.14
Res 47k | https://www.digikey.com/product-detail/en/stackpole-electronics-inc/RMCF0603JT47K0/RMCF0603JT47K0CT-ND/1943199 |  | Resistor | R5_ESC1, R5_ESC2, R5_ESC3, R5_ESC4, R5_ESC5, R5_ESC6, R5_ESC7, R5_ESC8 | J1-0603 | Res3 | 8 | 24 | 24 | 0.34
Res 2m | https://www.digikey.com/product-detail/en/stackpole-electronics-inc/CSS0603FT2L00/738-CSS0603FT2L00CT-ND/10719387 |  | 2 mOhms ±1% 3W Chip Resistor Nonstandard Anti-Sulfur, Automotive AEC-Q200, Current Sense, Moisture Resistant, Pulse Withstanding Metal Element | R6_ESC1, R6_ESC2, R6_ESC3, R6_ESC4, R6_ESC5, R6_ESC6, R6_ESC7, R6_ESC8 | WSL27262L000FEB | WSL27262L000FEB | 8 | 24 | 25 | 9.01
LTC4357CMS8#PBF | https://www.digikey.com/products/en?keywords=LTC4357CMS8%23PBF |  | Positive High Voltage Ideal Diode Controller, 9 to 80 V Vin, 8-pin SOP (MS8-8), 0 to 70 degC, Pb-Free | U1, U2 | LT-MS8-8_N | LTC4357CMS8#PBF | 2 | 6 | 6 | 24.78
TPS2481 | https://www.digikey.com/product-detail/en/texas-instruments/TPS2481PWR/296-27643-1-ND/2345432 |  | Positive voltage, intelligent protection device/hotswap controller and I2C current monitor | U3_ESC1, U3_ESC2, U3_ESC3, U3_ESC4, U3_ESC5, U3_ESC6, U3_ESC7, U3_ESC8 | TPS2481 | TPS2481 | 8 | 24 | 25 | 101.97
 |  |  |  |  |  |  |  |  |  | 305.29

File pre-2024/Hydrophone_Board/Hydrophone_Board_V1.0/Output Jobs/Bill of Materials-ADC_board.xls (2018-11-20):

Description | Designator | LibRef | Quantity | Value
Capacitor | C1_A1, C1_B1, C1_C1, C1_D1, C3_A1, C3_B1, C3_C1, C3_D1, C26_A2, C26_B2, C26_C2, C26_D2 | Cap | 12 | 6.2nF
Capacitor | C2_A1, C2_B1, C2_C1, C2_D1, C4_A1, C4_B1, C4_C1, C4_D1 | Cap | 8 | 3.9nF
Capacitor | C5_A1, C5_B1, C5_C1, C5_D1 | Cap | 4 | 4.06nF
Capacitor | C6, C7, C8, C9, C10, C11, C12, C13, C15, C18, C19 | Cap | 11 | 1uF
Capacitor | C14, C16, C17 | Cap | 3 | .1uF
Capacitor | C20, C22 | Cap | 2 | .47uF
Capacitor | C21, C23 | Cap | 2 | 33uF
Capacitor | C24, C25 | Cap | 2 | 10uF
BNC Elbow Connector | P1_A1, P1_B1, P1_C1, P1_D1 | BNC | 4
Header, 3-Pin | P4_A2, P4_B2, P4_C2, P4_D2 | Header 3 | 4
Header, 9-Pin | P_ADC | Header 9 | 1
Header, 5-Pin | P_Pot | Header 5 | 1
Header, 2-Pin | P_Vcc | Header 2 | 1
Resistor | R0 | Res3 | 1 | 0
Resistor | R1_A1, R1_B1, R1_C1, R1_D1 | Res3 | 4 | 5.49k
Resistor | R2_A1, R2_B1, R2_C1, R2_D1 | Res3 | 4 | 5.49k
Resistor | R3_A1, R3_B1, R3_C1, R3_D1 | Res3 | 4 | 422
Resistor | R4_A1, R4_B1, R4_C1, R4_D1 | Res3 | 4 | 422
Resistor | R5_A1, R5_B1, R5_C1, R5_D1 | Res3 | 4 | 324
Resistor | R6_A1, R6_B1, R6_C1, R6_D1 | Res3 | 4 | 324
Resistor | R7, R9, R11, R13, R17_A2, R17_B2, R17_C2, R17_D2, R18_A2, R18_B2, R18_C2, R18_D2 | Res3 | 12 | 10K
Resistor | R8, R10, R12, R14 | Res3 | 4 | 4.99K
Potentiometer | R15_A2, R15_B2, R15_C2, R15_D2, R16_A2, R16_B2, R16_C2, R16_D2 | RPot | 8 | 100K
 | U1_A1, U1_B1, U1_C1, U1_D1 | LT6234 | 4
 | U2 | MAXIM11043 | 1
 | U3_A2, U3_B2, U3_C2, U3_D2, U_AB1, U_CD1 | LM358DR | 6
 | U_Pot | AD5204 | 1
 | V1 | MAX6126 | 1
 | V2, V3 | LM3940 | 2

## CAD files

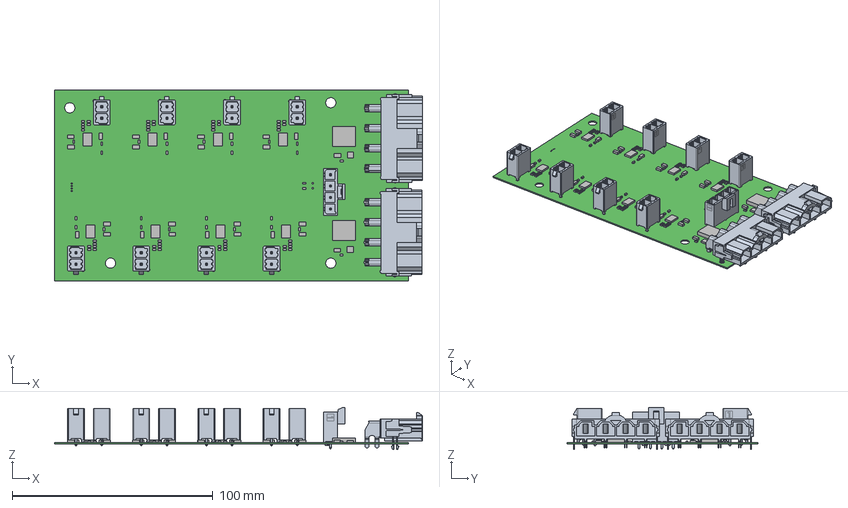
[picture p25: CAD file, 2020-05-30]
Merge_ESC_Board/Merge_ESC_Board.step
183.5 x 95.3 x 20.9 mm
Board
Extruded x 114

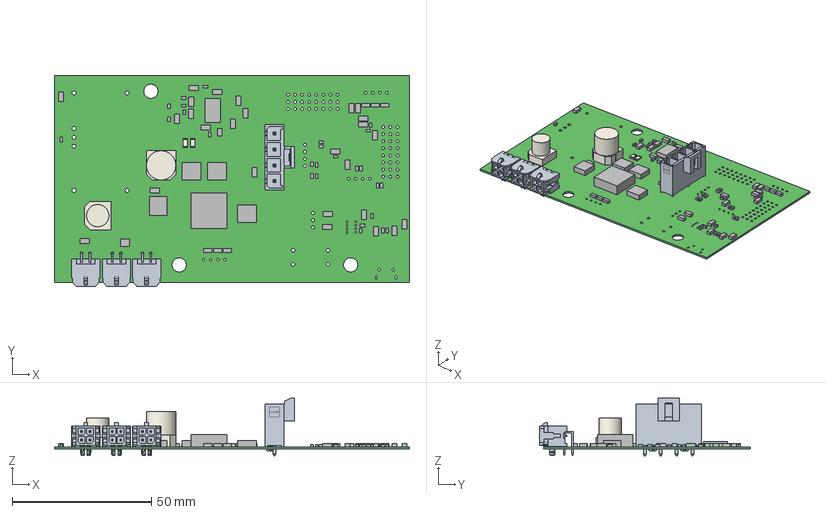
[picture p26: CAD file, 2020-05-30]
MiniSub_Power_Board/MiniSub_Power_Board.step
127.3 x 75.8 x 20.7 mm
Board
Extruded x 74

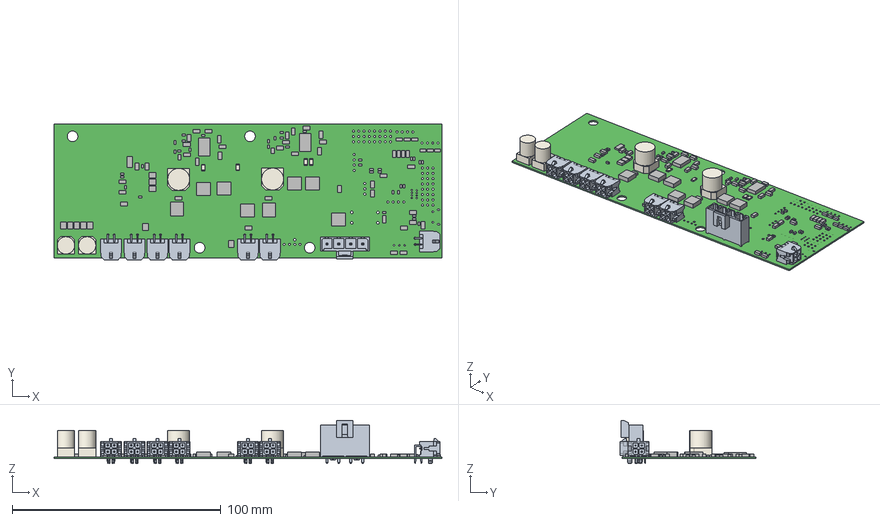
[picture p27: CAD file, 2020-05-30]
Power_Embedded_Board/Power_Embedded_Board.step
185.8 x 65.0 x 20.7 mm
Board
Extruded x 124

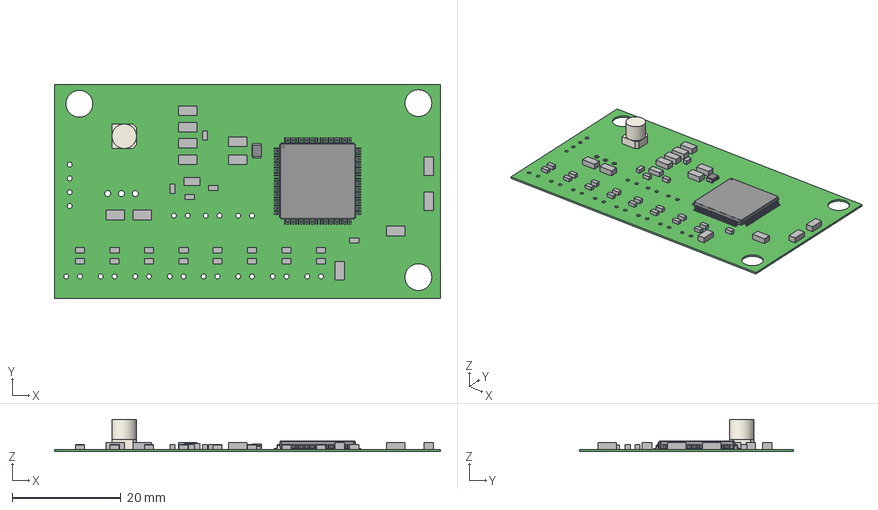
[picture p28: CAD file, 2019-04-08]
pre-2024/Pneumatics_Board/Pneumatics_Board.step
71.0 x 39.4 x 5.91 mm
Board
Extruded x 35
Open_CASCADE_STEP_translator_6.8_10.1.1
Lead x 2
BODY-QFP
LEAD-QFP x 100

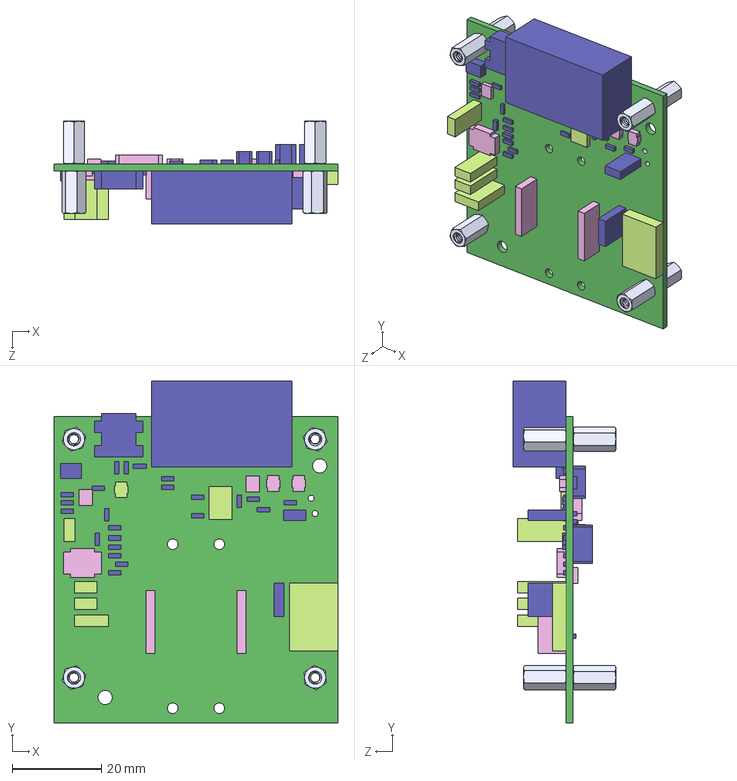
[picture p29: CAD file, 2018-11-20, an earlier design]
pre-2024/Electrical_Archive/Electrical 2017/Oceans_7 capstone/_Overview/Datasheets/IMU_s/Sparton Downloads/NDS-1-Solid-Model-Mechanicals.step
63.5 x 76.5 x 23.0 mm

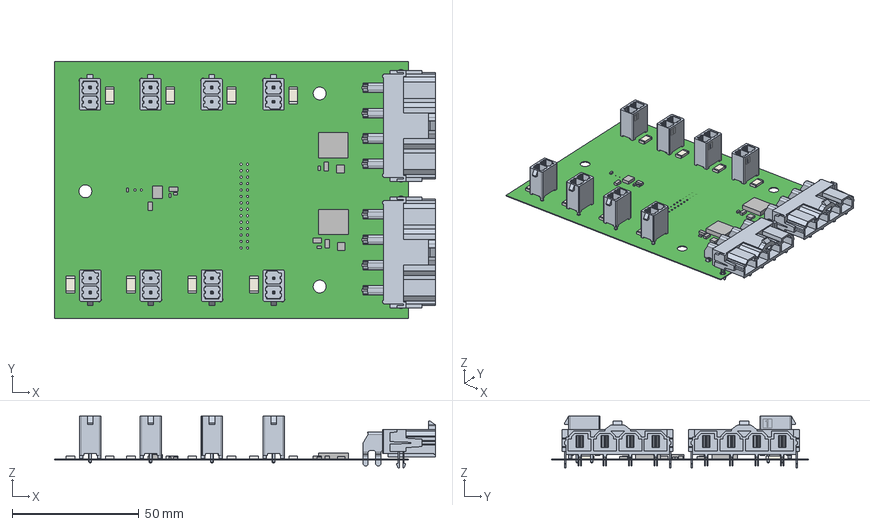
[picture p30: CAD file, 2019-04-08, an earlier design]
pre-2024/Electrical_Archive/Electrical 2019/Merge_ESC_Board/Merge_ESC_Board.step
150.4 x 101.6 x 20.4 mm
Board
Extruded x 39

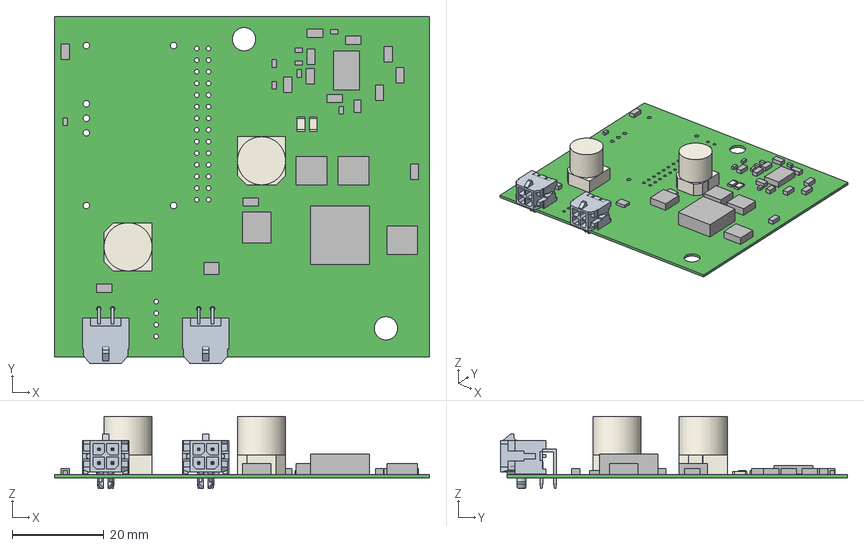
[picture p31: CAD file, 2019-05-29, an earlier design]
pre-2024/Electrical_Archive/Electrical 2019/MiniSub_Power_Board/MiniSub_Power_Board.step
81.9 x 75.8 x 15.8 mm
Board
Extruded x 37

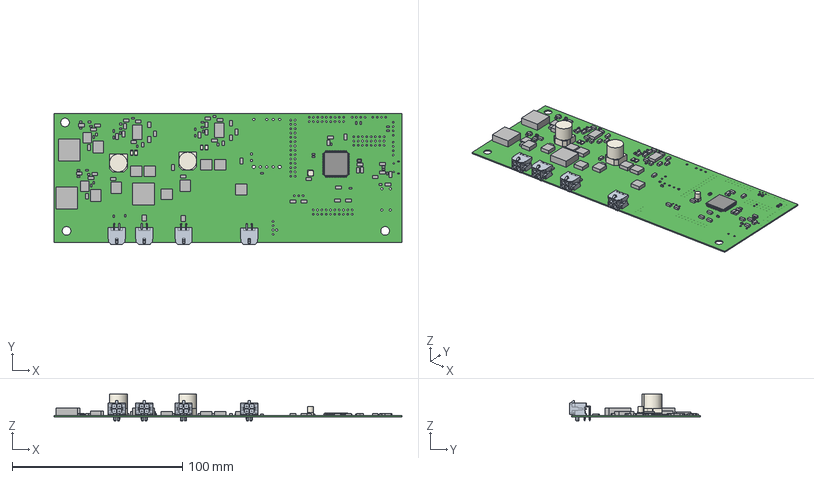
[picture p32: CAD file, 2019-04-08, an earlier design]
pre-2024/Electrical_Archive/Electrical 2019/Power_Embedded_Board/Power_Embedded_Board.step
204.6 x 77.1 x 15.8 mm
Board
Extruded x 124
Open_CASCADE_STEP_translator_6.8_10.1.1
Lead x 2
BODY-QFP
LEAD-QFP x 100

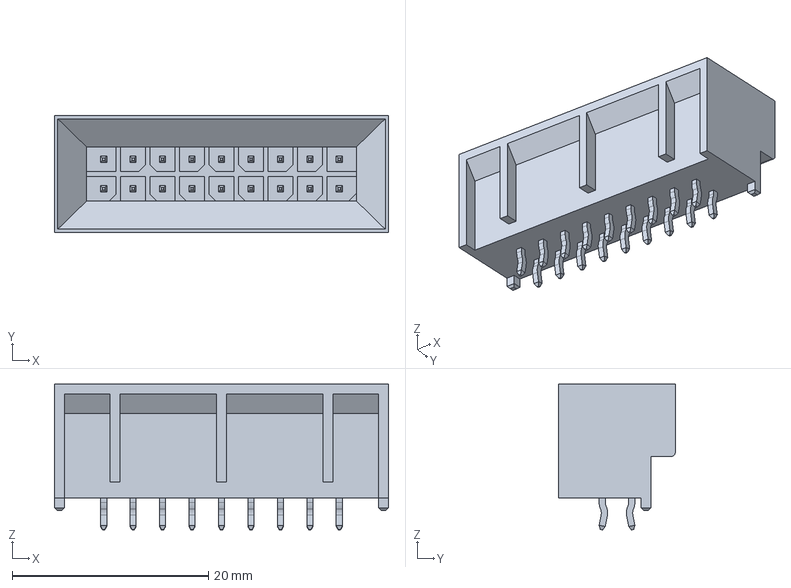
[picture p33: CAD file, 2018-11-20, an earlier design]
pre-2024/Electrical_Archive/Electrical 2018/Backplane/Backplane_V3.1_KH/parts/444321801.stp
34.0 x 11.9 x 14.9 mm

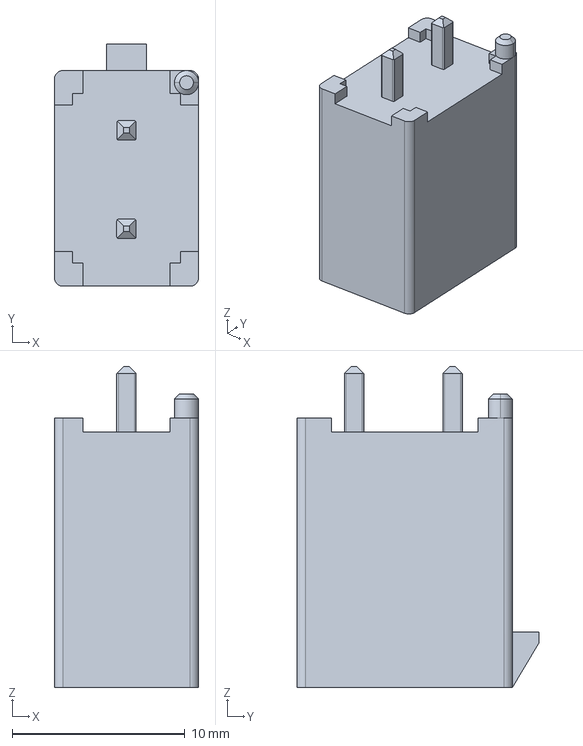
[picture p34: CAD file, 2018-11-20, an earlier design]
pre-2024/Electrical_Archive/Electrical 2018/Kill Switch/Kill_Switch_JV_V1.0.2/Parts/768290102.stp
8.35 x 14.0 x 18.6 mm

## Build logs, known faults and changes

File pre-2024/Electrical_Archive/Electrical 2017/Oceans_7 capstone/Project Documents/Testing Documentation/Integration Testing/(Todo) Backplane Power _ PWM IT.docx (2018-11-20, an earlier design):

Test Writer | | Kyle Harlow
Test Case Name | | Backplane Integration Test | | | | Test ID# | B-IT-1
Description | | Verify Voltage Outputs of Backplane and Connectivity of Power Board. Verify Voltage PWM of Backplane and Connectivity of Control Board | | | | Type | Black-Box

Test Information
Name of Tester | | | | | | Date
Hardware Version | | Backplane 1.0 | | | | Time
Setup | | Attach power supply, capable of providing up to 10A at 16V, to the high and ground terminals of the backplane. Set voltage output to 14.8V, the nominal voltage for the lithium ion batteries. Prepare multimeter to measure voltages up to 50V. Prepare oscilloscope to measure 5V PWM signals. Place Power Board in the Power Board slot on the Backplane. Place Control Board in the control board slot on the backplane. Connect USB to control board. Upload pwm output code. Set control board to send default 1.5ms PWM signals to all outputs. Turn on output of power supply.
Step | Action | Expected Results | Pass | Fail | N/A | Comments
1 | Measure voltage output on the 5V output connector | Output measures 5.0V +/- 0.1V
2 | Measure voltage output on the 12V output connector | Output measures 12V +/- 0.1V
3 | Measure voltage output on the 19V output connector | Output measures 19V +/- 0.1V
4 | Measure voltage output on the 48V, 1A output connector | Output measures 48V +/- 3V
5 | Measure voltage output on the 48V, 0.5A output connector | Output measures 48V +/- 3V
6 | Turn off power supply. Set voltage output to 16V. Repeat tests 1-5. | Voltage outputs are within the same tolerance for the original test sequence
7 | Turn off power supply. Set voltage output to 12.5V. Repeat tests 1-5. | Voltage outputs are within the same tolerance for the original test sequence
8 | Measure voltage output on the 14.8V output connector | Output measures 14.8V +/- 2.8V
9 | Enable PWM (see code header main.h for control strings) | None
10 | Measure outputs of PWM (1-8) Header | Output measures PWM 1.5+/-0.02ms pulse width per header
11 | Turn off and disconnect power supply from the board. Turn off multimeter. Remove Power Board from slot. Reset Control Board.Remove Control Board from slot. | None
Overall Results

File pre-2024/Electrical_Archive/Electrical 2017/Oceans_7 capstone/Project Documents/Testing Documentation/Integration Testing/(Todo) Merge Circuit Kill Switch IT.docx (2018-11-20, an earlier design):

Test Writer | | Abbigail Caballero
Test Case Name | | Merge Circuit Kill Switch Test | | | | Test ID# | MRG-IT-3
Description | | Verify that the kill switch shuts off the motors and sends a signal to the MCU verifying that motors have been switched off | | | | Type | Whitebox

Test Information
Name of Tester | | | | | | Date
Hardware Version | | Merge Circuit 1.0 | | | | Time
Setup | | Attach 14.8V power supply to merge circuit to the high and ground terminals of the battery inputs. Prepare multimeter for voltages up to 14.8V. Attach USB to Teensy and upload data polling code. Poll output of killswitch. Turn on output of power supply.
Step | Action | Expected Results | Pass | Fail | N/A | Comments
1 | Measure output of the kill switch with multimeter | Output measures 14.8V +/- 0.1V
2 | Measure output of kill switch with Teensy | Output measures Logic High
3 | Flip the mechanical killswitch | Output of killswitch is now 0V +/- 0.1V and signal from killswitch to MCU has gone from high to low
4 | Turn off power supply and disconnect from the board. Turn off multimeter. | None
Overall Results

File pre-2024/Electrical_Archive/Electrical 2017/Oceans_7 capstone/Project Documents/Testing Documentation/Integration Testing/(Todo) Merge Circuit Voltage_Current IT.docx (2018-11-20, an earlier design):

Test Writer | | Abbigail Caballero
Test Case Name | | Merge Circuit Voltage/Current Integration Test | | | | Test ID# | MRG-IT-1
Description | | Verify that the merge circuit is able to split the voltage correctly and supply each component with sufficient current | | | | Type | Whitebox

Test Information
Name of Tester | | | | | | Date
Hardware Version | | Merge Board 1.0 | | | | Time
Setup | | Attach two 14.8V 100A Lithium Ion Polymer batteries to Merge Circuit Board. Attach power load to each output being measured. Prepare multimeter for voltages up to 14.8V and currents up to 30A. Attach load to Motor 10. Plug in Teensy via USB to testing computer. Load ADC_Merge.ini to Teensy. Reset Teensy to initialize. Open serial terminal on testing computer. Set kill switch to active mode. Turn on power load.
Step | Action | Expected Results | Pass | Fail | N/A | Comments
1 | Measure voltage outputs to the current sensing resistors | Each output measures 14.8±0.4V
2 | Measure output of 5V switching regulator | Output measures 5±0.3V
3 | Observe terminal printout | UART Terminal receives serial data from Teensy, prints to screen
4 | Measure current through output of current sensing resistors with power load attached to individual outputs of the merge circuit to the motors | Motor 10 load measures 30A
5 | Move the load to Power Output Rail 2.Measure current through the output of current sensing resistor with power load attached to output of the the merge circuit to the conversion board | Power Output Rail 2 load measures 20A
6 | Move the load to Motor 5 output. Measure current through output of current sensing resistors with power load attached to output of the merge circuit to the backplane | Motor 5 load measures 10A
Overall Results

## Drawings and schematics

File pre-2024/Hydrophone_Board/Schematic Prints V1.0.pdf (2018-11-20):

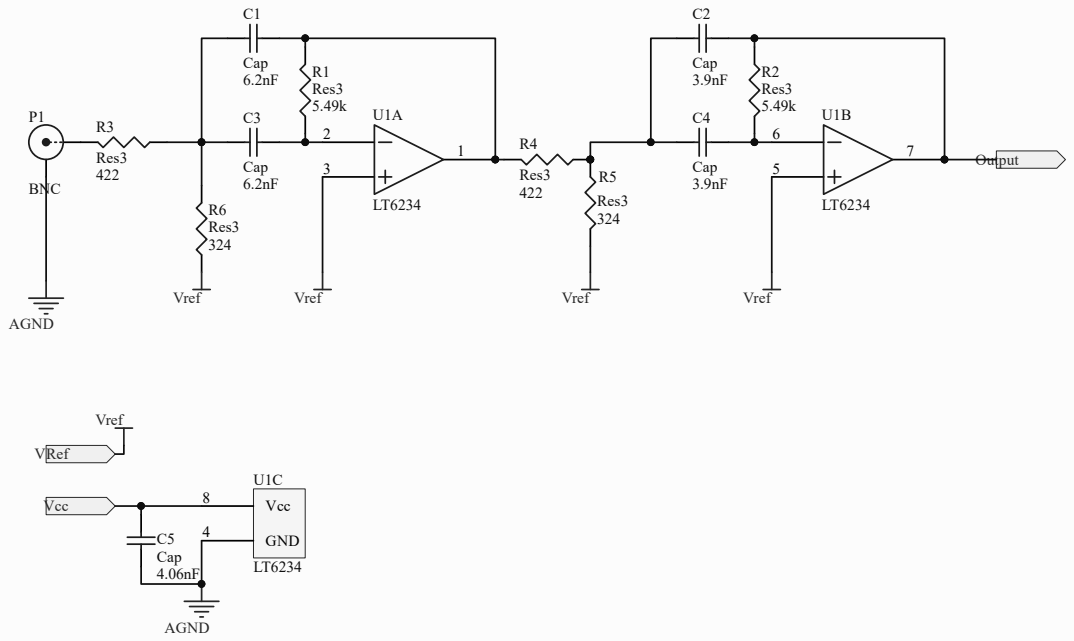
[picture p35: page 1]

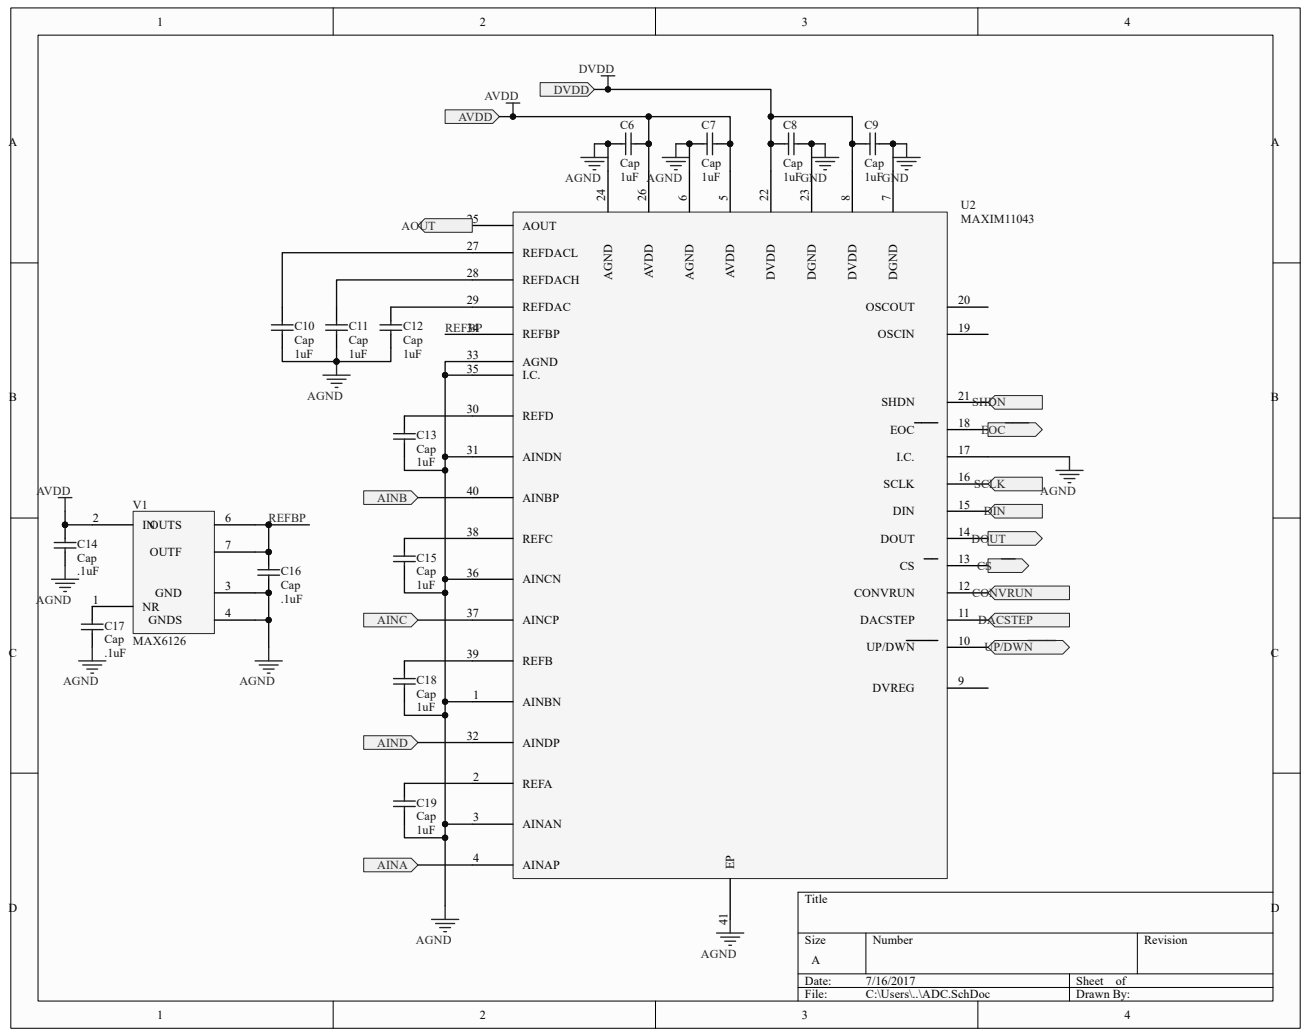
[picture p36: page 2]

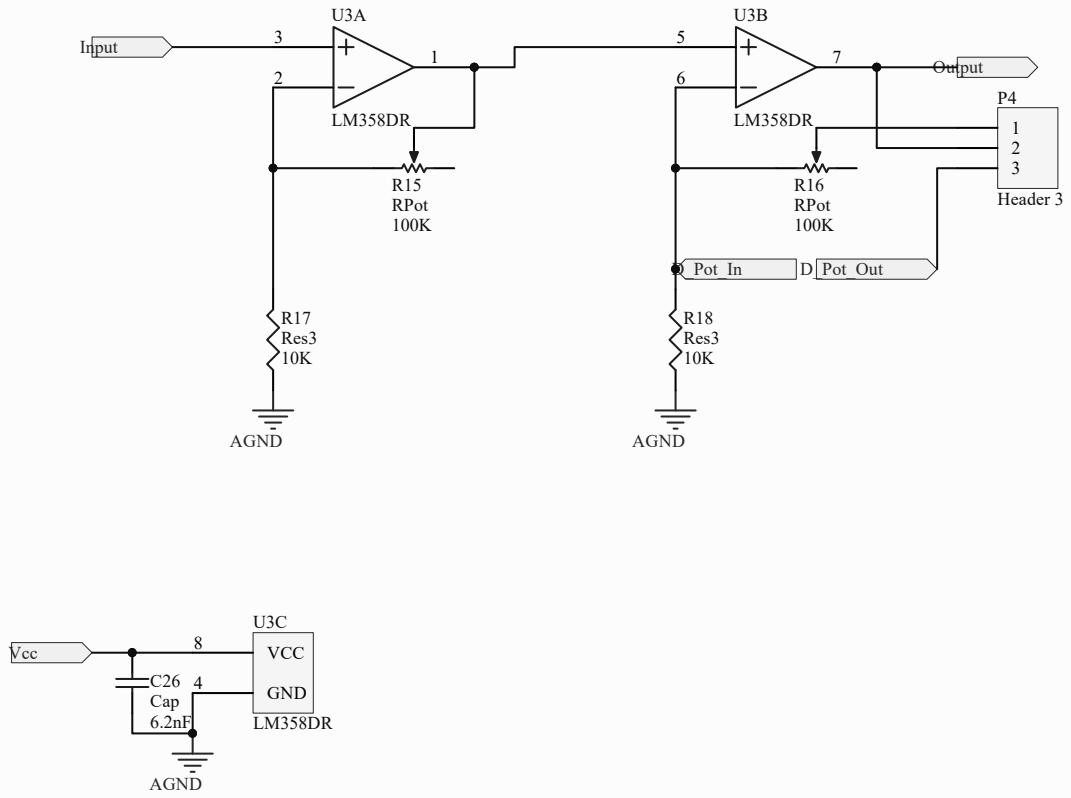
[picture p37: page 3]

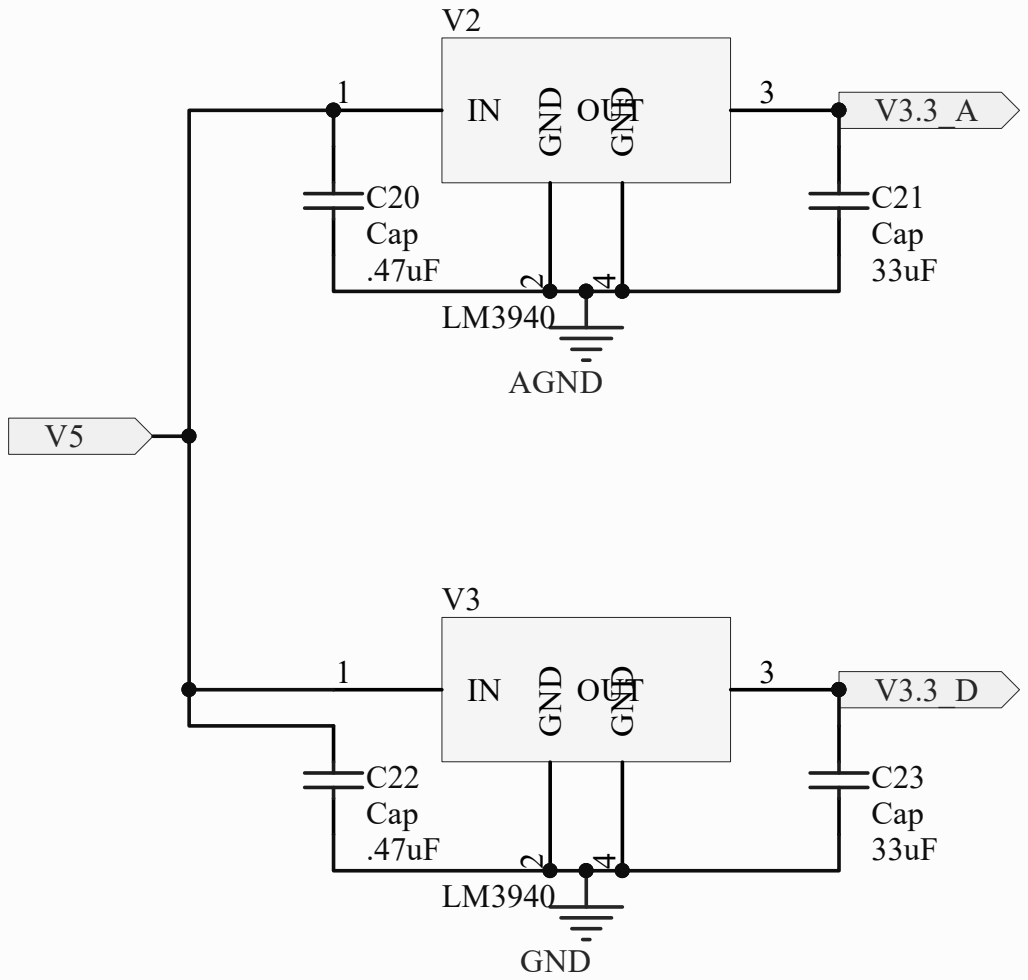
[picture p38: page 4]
Title; Size; Number; Revision; File:; C:\Users\..\Power.SchDoc; Drawn By:; AGND; GND; OUT; C20 Cap; C21 Cap; C22 Cap; C23 Cap

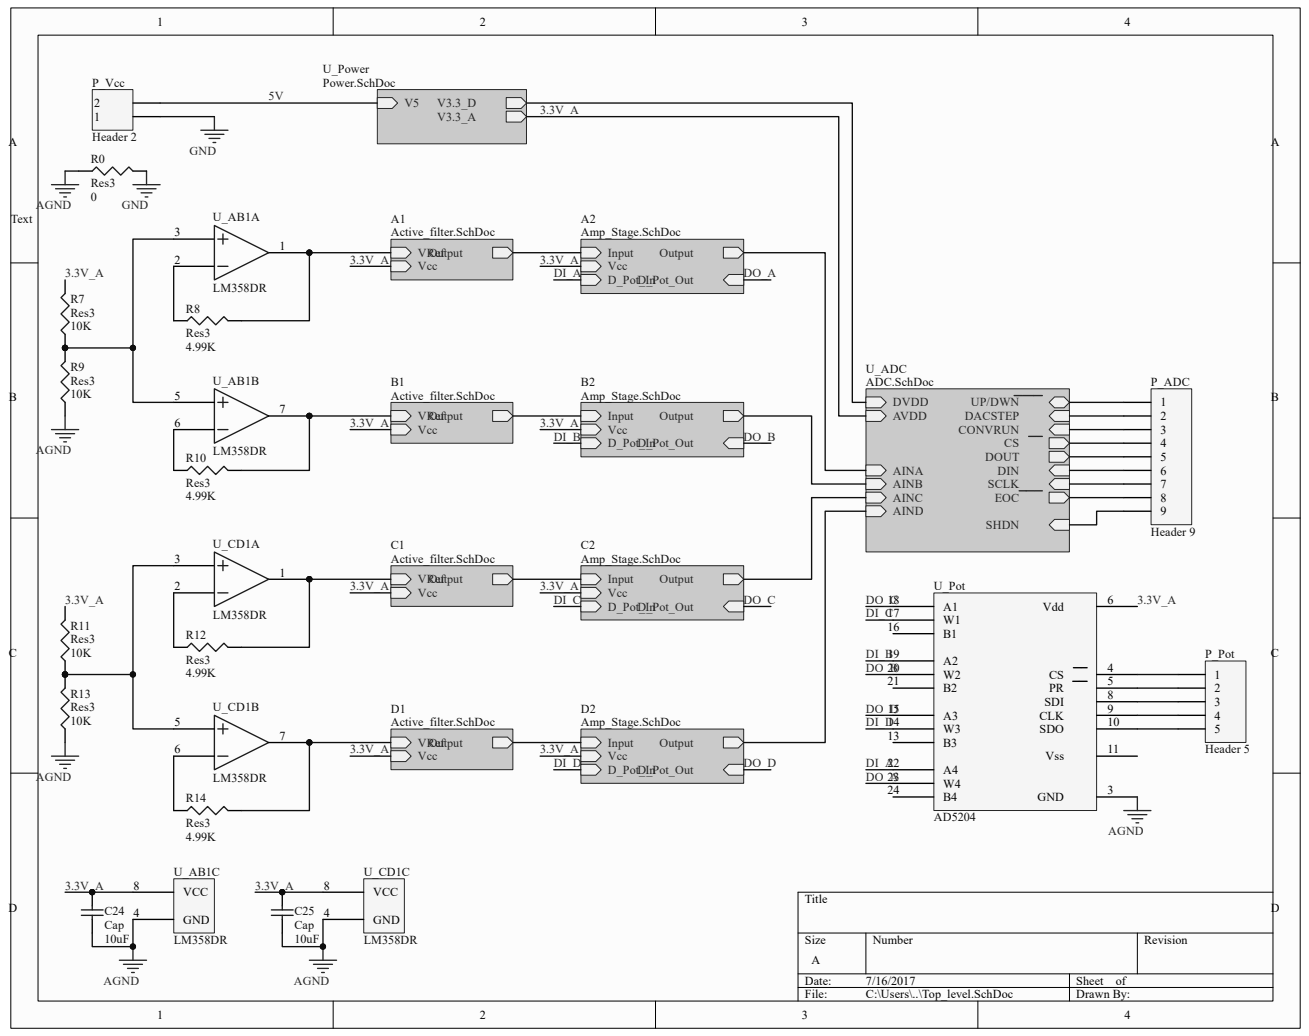
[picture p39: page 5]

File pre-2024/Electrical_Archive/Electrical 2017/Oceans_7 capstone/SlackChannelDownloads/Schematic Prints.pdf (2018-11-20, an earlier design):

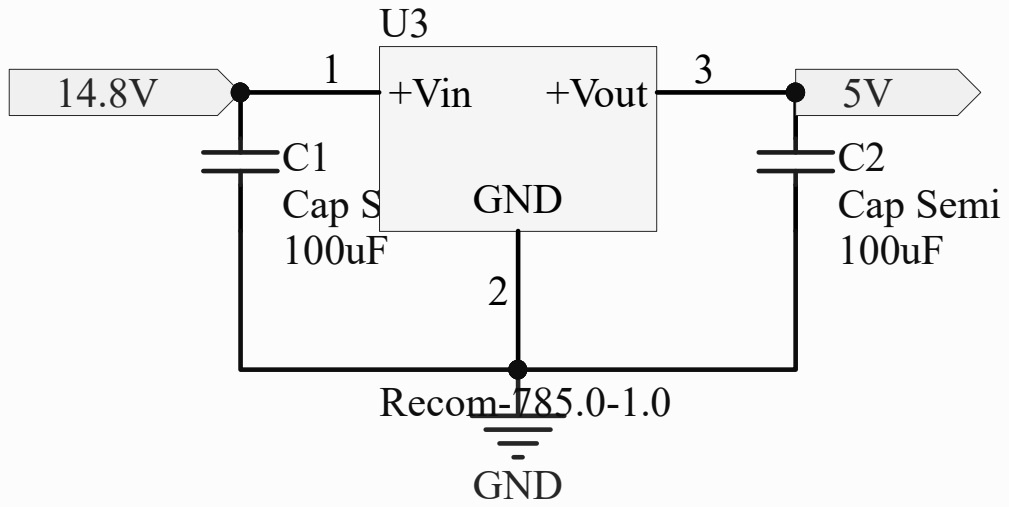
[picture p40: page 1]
Title; C1 Cap Semi; C2 Cap Semi; GND; +Vin; +Vout; Recom-785.0-1.0

Size A | Number | Revision

Date: 2/21/2017 | Sheet of
File: C:\Users\..\5V_Converter.SchDoc | Drawn By:

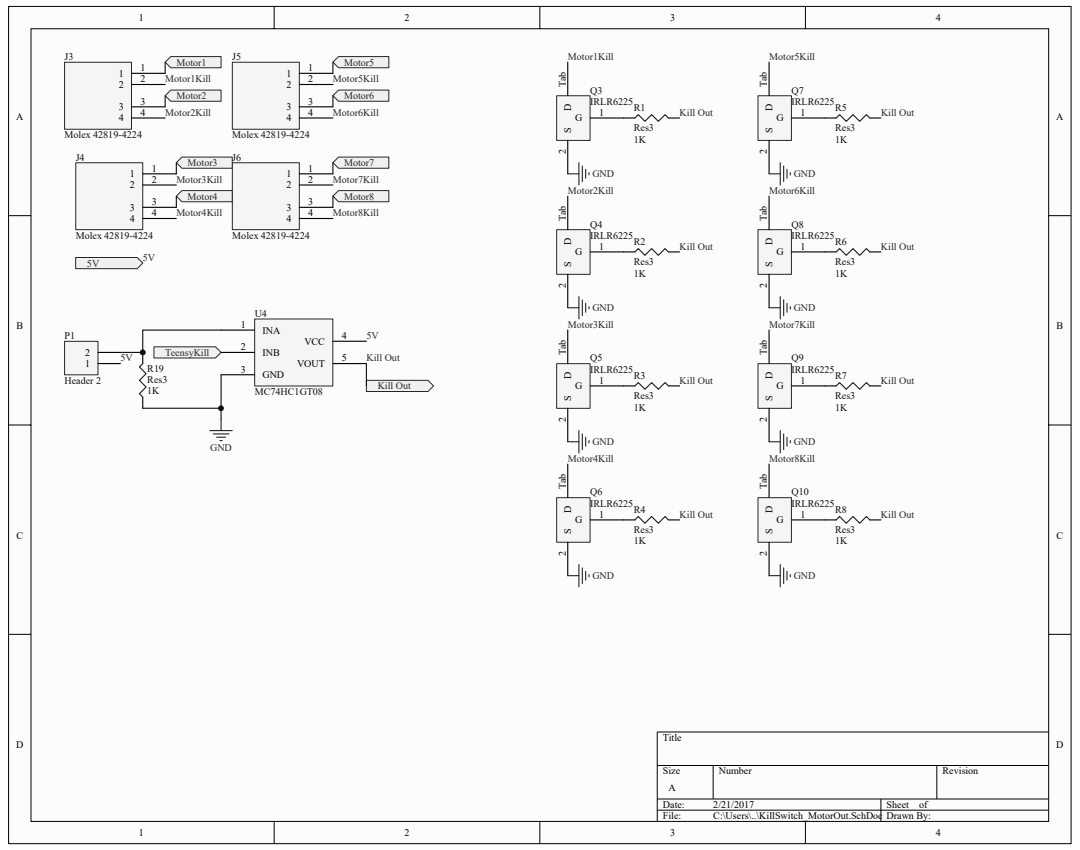
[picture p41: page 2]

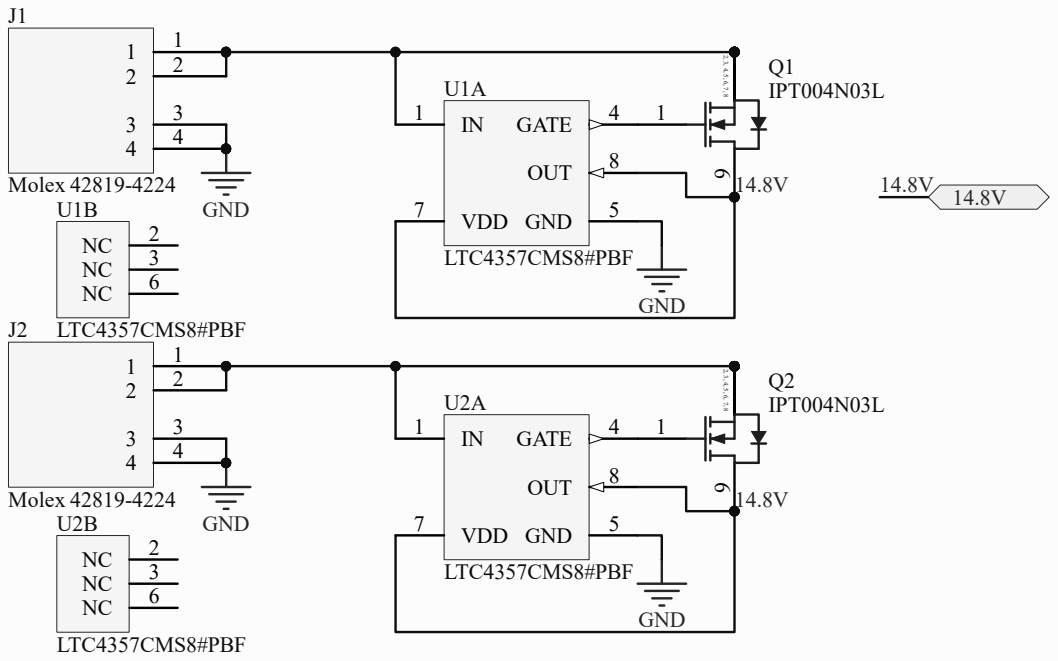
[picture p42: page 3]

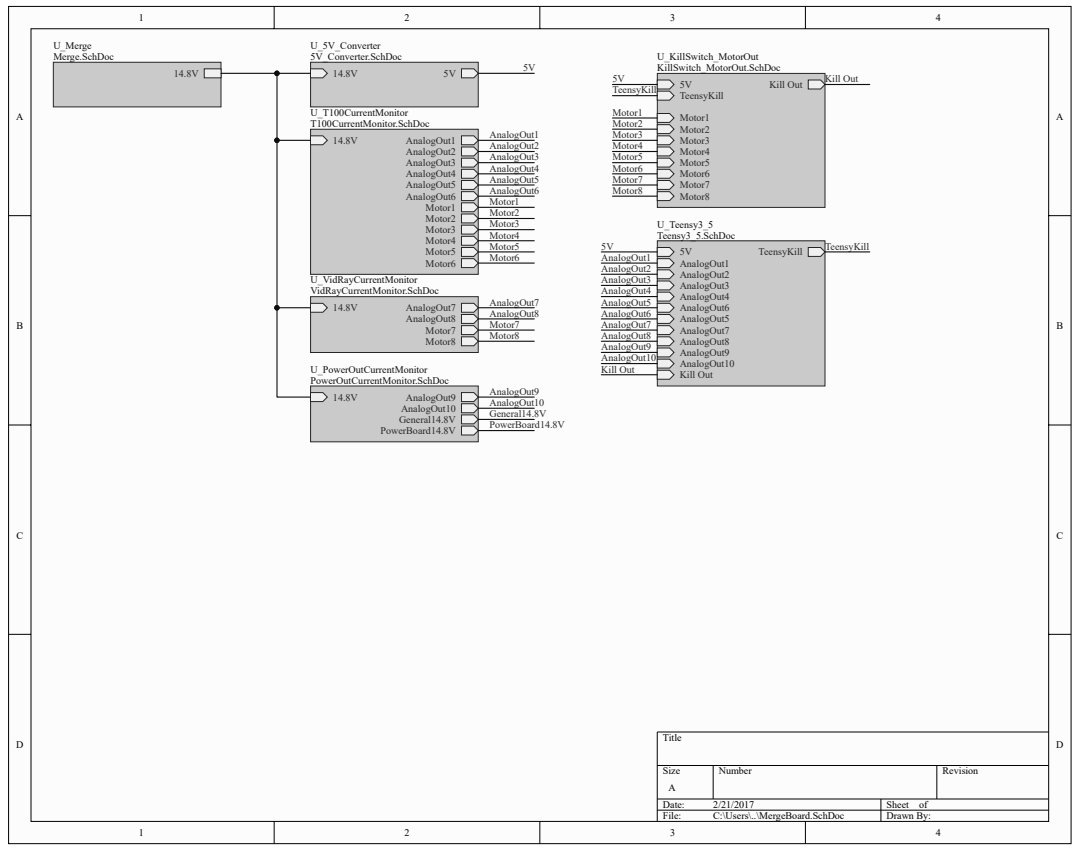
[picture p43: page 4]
Title; Size; Number; Revision; File:; C:\Users\..\MergeBoard.SchDoc; Drawn By:; U_5V_Converter 5V_Converter.SchDoc; AnalogOut1 AnalogOut2 AnalogOut3 AnalogOut4 AnalogOut5 AnalogOut6 Motor1 Motor2 Motor3 Motor4 Motor5 Motor6; U_T100CurrentMonitor T100CurrentMonitor.SchDoc; AnalogOut7 AnalogOut8 Motor7 Motor8; U_VidRayCurrentMonitor VidRayCurrentMonitor.SchDoc; General14.8V PowerBoard14.8V; AnalogOut9; AnalogOut10; U_PowerOutCurrentMonitor PowerOutCurrentMonitor.SchDoc; TeensyKill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

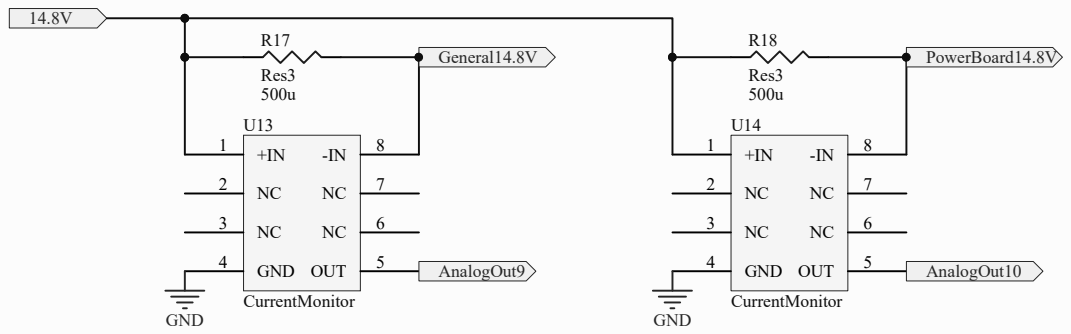
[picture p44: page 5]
Title; Size; Number; Revision; File:; C:\Users\..\PowerOutCurrentMonitor.SchDoc Drawn By:; GND 4; OUT; CurrentMonitor; Res3; GND; General14.8V; PowerBoard14.8V; AnalogOut9; AnalogOut10

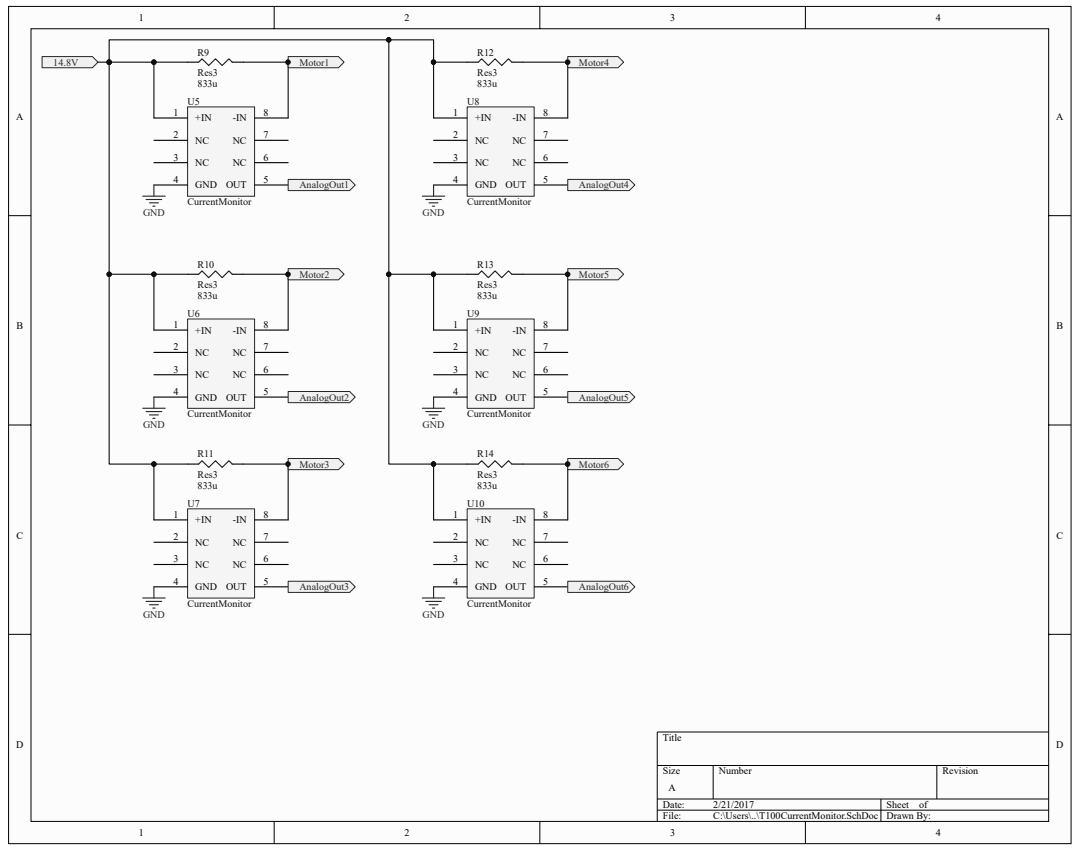
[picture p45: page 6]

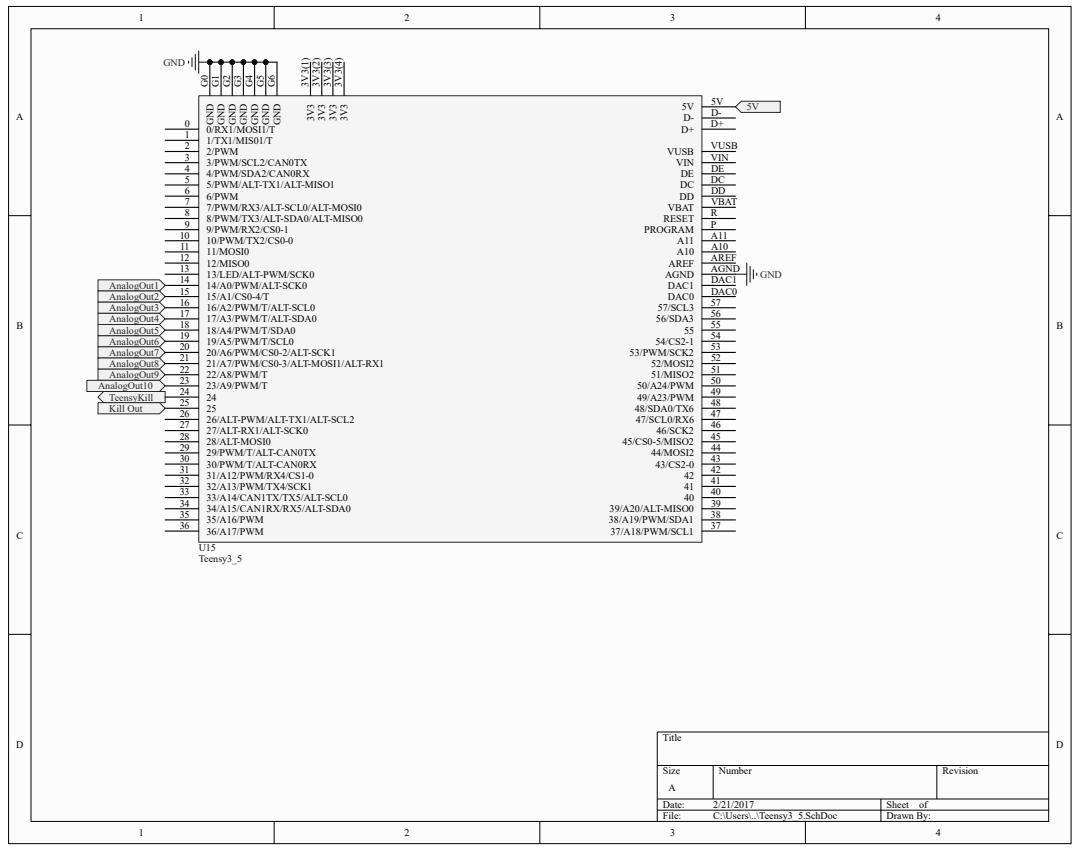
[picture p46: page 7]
Title; Size; Number; Revision; File:; C:\Users\..\Teensy3_5.SchDoc; Drawn By:; TeensyKill; GND; AnalogOut1 AnalogOut2 AnalogOut3 AnalogOut4; AnalogOut6; AnalogOut5; AnalogOut7 AnalogOut8; Kill Out; AnalogOut9 AnalogOut10; GND G0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

Title; Size; Number; Revision; File:; C:\Users\..\VidRayCurrentMonitor.SchDocDrawn By:; GND 4; OUT; CurrentMonitor; Res3; GND; AnalogOut7; AnalogOut8; Motor7; Motor8

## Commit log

2018-11-20 Created repository with all PCB and datasheet files
    [12V_Converter 3_6_2018.SchDoc, 12V_Converter.SchDoc, 19V_Converter.SchDoc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]
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2018-11-22 Cleaned up power board libraries and schematics
    1. Created a library with all of the power/embedded board
    components and replaced all parts on power schematics to assure
    that all parts are from the libraries.
    2. Cleaned up the schematics to make them look better and to
    make sure all parts are linked to a footprint.
    3. TODO: Finish the top schematic and make sure all connections
    between power board and other boards exist.
    [12V_Converter.SchDoc, 19V_Converter.SchDoc, 48V_Converter.SchDoc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]
2018-12-01 Initialized pneumatics board project with empty files
    [Pneumatics_Board.PcbDoc, Pneumatics_Board.PrjPcb, Pneumatics_Board.SchDoc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]
2018-12-01 Created part libraries for the pneumatics board
    [Pneumatics_Board_Library.PcbLib, Pneumatics_Board_Library.SchLib]
2018-12-02 Completed Pneumatics board libraries and schematic
    [Embedded_Chip.SchDoc, Pneumatics_Board.PcbDoc, Pneumatics_Board.PrjPcb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]
2018-12-05 Edited some of the schematics for power board
    [12V_Converter.SchDoc, Embedded_Chip.SchDoc, Embedded_System_Top.SchDoc]
2018-12-07 Added to Power/Embedded Board Schematics
    Still need to update 3x8 header footprint and add the Molex
    Connector footprint for outputs.
    [12V_Converter.SchDoc, 19V_Converter.SchDoc, 48V_Converter.SchDoc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]
2018-12-07 Updated power board. Needs work on 48V converter.
    [19V_Converter.SchDoc, 48V_Converter.SchDoc, 9V_Converter.SchDoc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]
2018-12-07 Updated Merge Board to reflect work completed this semester
    [768290102.stp, AD8217_DT.PcbLib, AD8217_DT.SchLib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]
2018-12-08 Completed the pneumatics board layout.
    Still need to create gerber files and order board.
    [Embedded_Chip.SchDoc, Pneumatics_Board.PcbDoc, Pneumatics_Board.PrjPcb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]
2018-12-21 Finished power schematics and updated merge schematics
    1. Power/Embedded board schematics are completed and components
    have been imported to a PCB document. Parts still need to be
    laid out and routed.
    2. Condensed the multiple parts libraries of the merge board into
    a single parts library for ease of use.
    3. Updated merge board schematics to change the file names to
    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
    [12V_Converter.SchDoc, 19V_Converter.SchDoc, 48V_Converter.SchDoc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]
2018-12-21 Created pneumatics gerbers and updated power board design rules
    1. Finished pneumatics board gerber files and used the Advanced
    Circuits rule checking tool to touch up the PCB files and
    assure that all files are printable.
    2. Changed Power/Embedded board design rules to avoid the rule
    violations which were present in the pneumatics board.
    [Pneumatics_Board.PcbDoc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]
2018-12-24 Changed a few components to match parts on digikey for the BOM
    [19V_Converter.SchDoc, 9V_Converter.SchDoc, Embedded_Chip.SchDoc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]
2019-02-08 Finalized Pneumatics board and Kill Switch Testing Board
    1. Added final changes to pneumatics board, board is ready to
    print.
    2. Created kill switch testing board to test high side kill switch
    and potential transistor options.
    [Kill_Switch_Testing.PcbDoc, Kill_Switch_Testing.PcbLib, Kill_Switch_Testing.PrjPcb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]
2019-02-08 Added zip files for the fabrication outputs
    [Kill_Switch_Testing.GKO, Kill_Switch_Testing.GTL, Kill_Switch_Testing.GTO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]
2019-02-25 Layed out board. Fixed some resistor and header footprints.
    [19V_Converter.SchDoc, 48V_Converter.SchDoc, 48V_Converter2.SchDoc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]
2019-02-28 Finalized power board (No temp sensor)
    [Power_Embedded_Board.PcbDoc, Power_Embedded_Board_Top.SchDoc]
2019-03-16 Pneumatics board Rev 2 and Merge board updates
    1. Added the leak sensor circuit to the pneumatics board and made
    more room around the mounting holes for screws, completing
    revision 2.
    2. Added the kill switch circuitry to the merge board, still need
    to figure out how to properly use repeated sheets for the ESC
    headers because they are not connecting properly when added to
    the PCB layout.
    [ESC_Header.SchDoc, Embedded_Chip.SchDoc, Merge_ESC_Board.PrjPcb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]
2019-03-22 Fixed trace width spacing.
    [Power_Embedded_Board.PcbDoc, Power_Embedded_Board.PrjPcb]
2019-03-26 Fixed annular ring sizes.
    [Power_Embedded_Board.PcbDoc, Power_Embedded_Board.PrjPcb, Power_Embedded_Board_Library.PcbLib]
2019-04-08 Finalized all main sub boards and started mini sub power board.
    1. Completed all main sub board layouts and verified them against
    the Advanced Circuits rule checker.
    2. Created fabrication outputs of all main boards and zipped them
    in their corresponding Board_Fabrication folder.
    3. Created step files of each main sub board for mechanical CAD
    design involving the boards.
    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
    [19V_Converter.SchDoc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]
2019-05-26 Added sheet numbering and titles
    [12V_Converter.SchDoc, 19V_Converter.SchDoc, 48V_Converter.SchDoc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]
2019-05-26 MiniSub 5V converter added
    [19V_Converter.SchDoc, 5V_Converter.SchDoc, MiniSub_Power_Board.PcbDoc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]
2019-05-27 MiniSub power board initial layout
    [12V_Converter.SchDoc, 19V_Converter.SchDoc, MiniSub_Power_Board.PcbDoc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]
2019-05-27 MiniSub power board draft complete
    [MiniSub_Power_Board.PcbDoc]
2019-05-29 MiniSub Project Exports and completion
    [5V_Converter.SchDoc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]
2019-10-18 Copied 2019 Electrical stuff into the Archive folder.
    [12V_Converter.SchDoc, 19V_Converter.SchDoc, 24-SOIC.PcbLib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]
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2019-11-06 Updated 9V converter schematic.
    [9V_Converter.SchDoc, Power_Embedded_Board.PrjPcb, Power_Embedded_Board_Library.PcbLib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]
2019-11-08 Revised Merge board
    1. Switched to I2C current sensing chips for each motor from the old
    analog current sense amplifiers. This should increase our noise
    tolerance when reading the motor currents.
    2. Used a combined MOSFET driver and current sensing IC to allow for
    automatic shut down of a motor if it pulls too much current.
    [ESC_Header.SchDoc, Kill_Switch_Testing.PcbDoc, Kill_Switch_Testing.PcbLib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]
2019-11-15 Updated 48V converter schematic.
    [48V_Converter.SchDoc, 48V_Converter2.SchDoc, Power_Embedded_Board.PrjPcb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]
2019-11-15 Fixed small issue with 48V simulation.
2019-11-15 Added Pearl Geck library parts.
    [Power_Embedded_Board_Library.PcbLib, Power_Embedded_Board_Library.SchLib]
2019-11-16 Updated embeded system schematic.
    [Embedded_Chip.SchDoc, Embedded_Circuits.SchDoc, Embedded_System_Top.SchDoc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]
2020-02-03 Finished Merge board layout. Started power board layout.
    [12V_Converter.SchDoc, 19V_Converter.SchDoc, 48V_Converter.SchDoc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]
2020-02-28 Added embeded system schematics to minisub power board.
    [12V_Converter.SchDoc, Embedded_Chip.SchDoc, Embedded_Circuits.SchDoc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]
2020-02-28 Fixed schematic issuse. Continued layout.
    [12V_Converter.SchDoc, 19V_Converter.SchDoc, 48V_Converter.SchDoc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]
2020-03-10 Fixed issues in schematic. Changed to 4 layer layout.
    [ESC_Header.SchDoc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]
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2020-08-02 Fixed first bugs with merge board and general cleanup
    View Adjustments
    * Trasparent 2D View
    * Dark Green 3D View
    * Hide layers that are not usefull for general inspection
    Fixed Layer Stackup
    * Inners to 1/2 OZ
    * Used JLC7628 Stackup (see https://cart.jlcpcb.com/impedance)
    Designators
    * Changed room naming to Channel Alpha
    Room Generation
    * Disabled room generation for top level sheet
    Net Naming
    * Changed VCC to VBAT_4S_MERGED
    * Added names for input power nets
    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
    [ESC_Header.SchDoc, Merge_ESC_Board.PcbDoc, Merge_ESC_Board.PrjPcb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]
2020-08-08 Added 3D bodies, fixed collisions
    [Embedded_Circuits.SchDoc, Merge_ESC_Board.PcbDoc, Merge_ESC_Board.PrjPcb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]
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2024-10-22 Uploaded DVL files
    For future versions:
    - switch micro USB type b female connector to include mechanical holes/cutout layers
    - downsize resistor and capacitors from 1206 to 0805 or 0603
    [DVL_BOM.xlsx, DVL_Interface.SchDoc, DVL_InterfaceRevA.PcbDoc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]
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2024-12-03 Updated Files
    - added mechanical holes to micro B connector
    - widened power traces
    - cleaned silkscreen
    [DVL_Interface.SchDoc, DVL_InterfaceRevA.PcbDoc, RobosubDVLInterface.PrjPcb]
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
